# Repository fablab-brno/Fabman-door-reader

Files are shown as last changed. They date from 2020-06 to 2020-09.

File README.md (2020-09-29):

# Fabman door reader

This repository is for Fabman door reader. This device and firmware were designed and developed by FabLab Brno. 

You can find here: 
 - PCB data for all revision of HW 
 - STL files for case
 - design files of the case for Fusion 360
 - source code of the firmware for this device 
 - images of assembled board and images of the case
 
We used Arduino IDE for development of this firmware. 

You will need these libraries to compile FW from source code: 
 - ArduinoJson (v. 6.13.0 in Library Manager)
 - WiFiManager (https://github.com/tzapu/WiFiManager/tree/development)- install it in IDE from ZIP file
 - SimpletTimer (https://github.com/jfturcot/SimpleTimer) - install it in IDE from ZIP file
 - SmartLeds (https://platformio.org/lib/show/1740/SmartLeds) - install it in IDE from ZIP file

#### This firmware include following:

- [x] OTA update
- [x] WiFiManager - you can setup your WiFi network for OTA updates, API key for Fabman bridge, name of the device, ID of the device and if connection type (WiFi/Ethernet) 

If somebody swipe their card and device is properly set to use Fabman service, it will send standart query and behave on received data. There is also option (which we use, but it is not default behaviour) to check, if member has **any** actvive package, and if so,it will be allowd to use door. This behaviour must be set by bollean variable (checkOH in config.h file) and FW must recompiled and flashed again in to the device. I will try to add this as option via WiFiManager in the future.  
OTA updates are available, but you must have some server where you can store text and bin files. Device check for new FW update at every start. 

#### HW include following: 

 - RGB LED (WS2812B) - which indicate status of the device (breathing blue - idle, green - allowed access, red - denied access, orange - WiFiManager setup process)
 - 12V to 5V voltage converter based on MP1584EN
 - 3-pin connector for 12V power connection (+12V, GND, GND for lock)
 - 2-pin connector for security alarm (optional). This is normaly closed when cover is closed as screw is pushing towards tactile switch. If somebody open the cover, switch will be released and external alarm system should trigger some alert.    
 - Security button
 - 3-pin JST connector for RFID data. This one is connected to the GWIOT 7941E RFID module which sends data via UART connection (9600 bauds). There is 5V, DATA and GND.  
 - 5V DC relay G6L-1F-DC5 which connect GND to the lock in the door. Positive voltage must be connected to the door directly.
 - 4-pin connector for UART. There is 5V, GND, RX and TX connection and this connector is used for programming and debugging.
 - Reset button
 - Boot button
 - Setup button - if you hold this button when device is powered on or reseted, it will call function which will turn on AP mode in ESP32 and will fire up web server with default address **192.168.4.1**. 

You can find some images of the board, 3D printed case and whole assembly in **/img** folder.
  
#### There are these revision of the board:

**rev. A**

First version of the board. Step-down converter is not working (wrong layout). RGB LED need bodge wire to the IO4 on ESP32. Everything else is working. 

**rev. B** 

Step-down converter is now using reference design for MP1584EN. RGB LED connection fixed. Relay and 3-pin JST connector moved to bottom side to save some height. Added setup button for WiFiManager. Added 6-pin connector to connect LAN module via SPI bus. This was working but LAN module (ENC28J60) does not supprt SSL connection.

**rev. C**

6-pin connector changed for 14-pin connector which support LAN8720 module. This module is supported by Arduino-ESP32 development tools. This as tested and it is working. **This board does not support PoE**. 

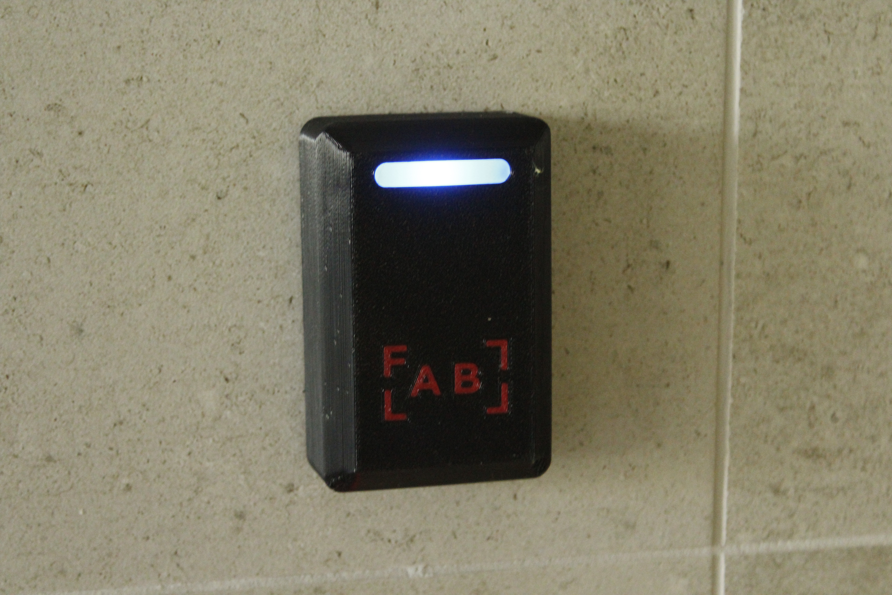
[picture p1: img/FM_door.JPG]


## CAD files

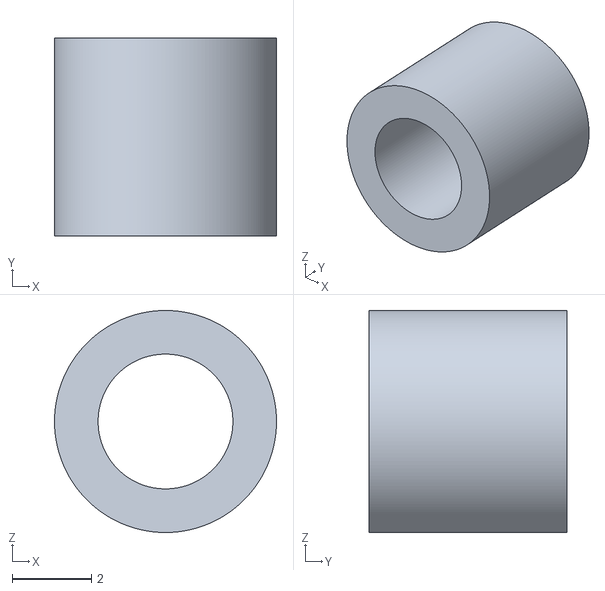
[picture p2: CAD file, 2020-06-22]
HW/STL/FM_door_standoff.stl
5.60 x 5.00 x 5.60

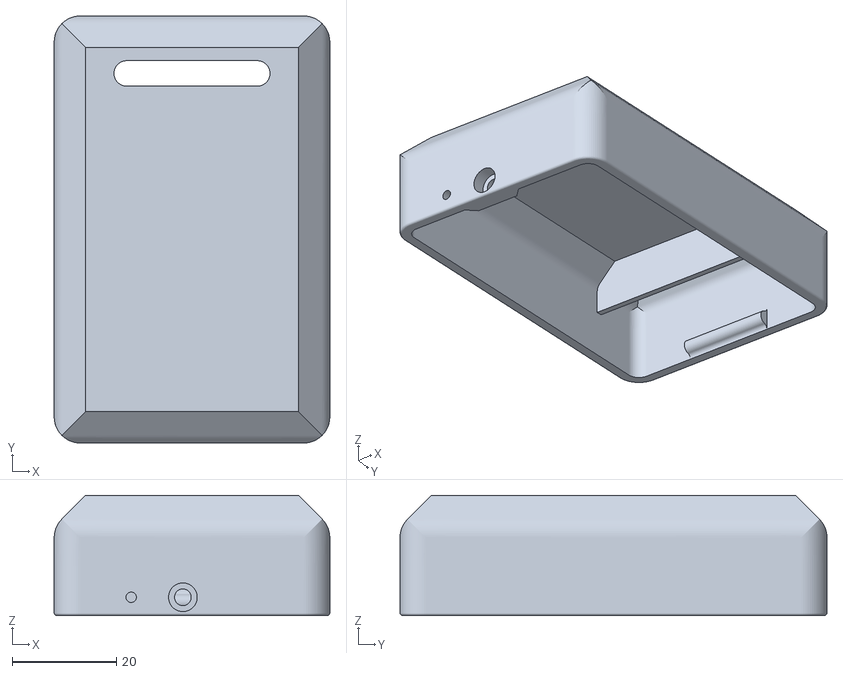
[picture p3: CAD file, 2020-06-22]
HW/STL/FM_door_front_cover_no_logo.stl
52.8 x 81.8 x 23.0

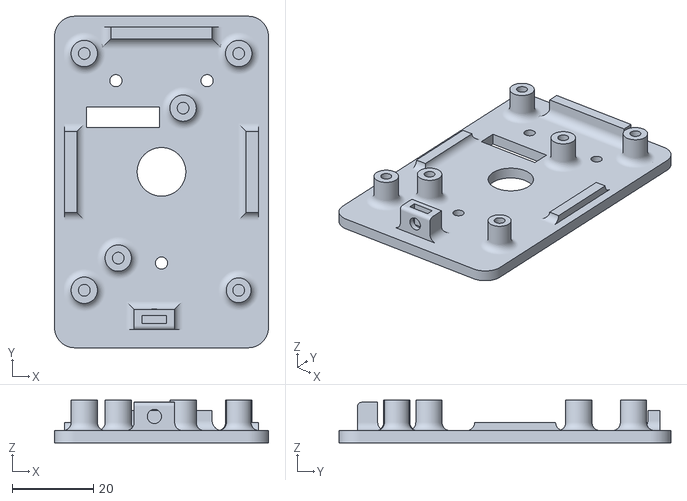
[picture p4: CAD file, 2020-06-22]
HW/STL/FM_door_back_plate.stl
52.8 x 81.8 x 10.5

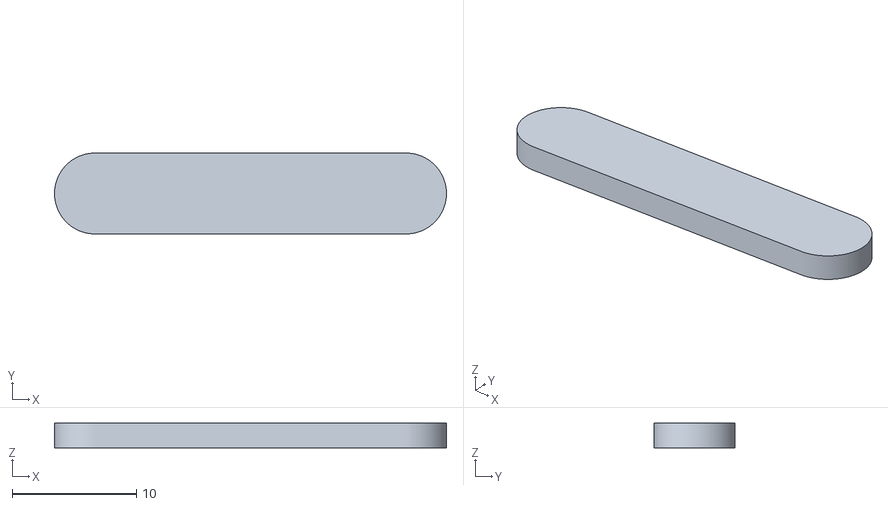
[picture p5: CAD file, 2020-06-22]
HW/STL/FM_door_diffusor.stl
31.5 x 6.50 x 2.00

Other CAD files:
HW/STL/FM_door_front_cover.stl
HW/FM_door_assembly.f3z

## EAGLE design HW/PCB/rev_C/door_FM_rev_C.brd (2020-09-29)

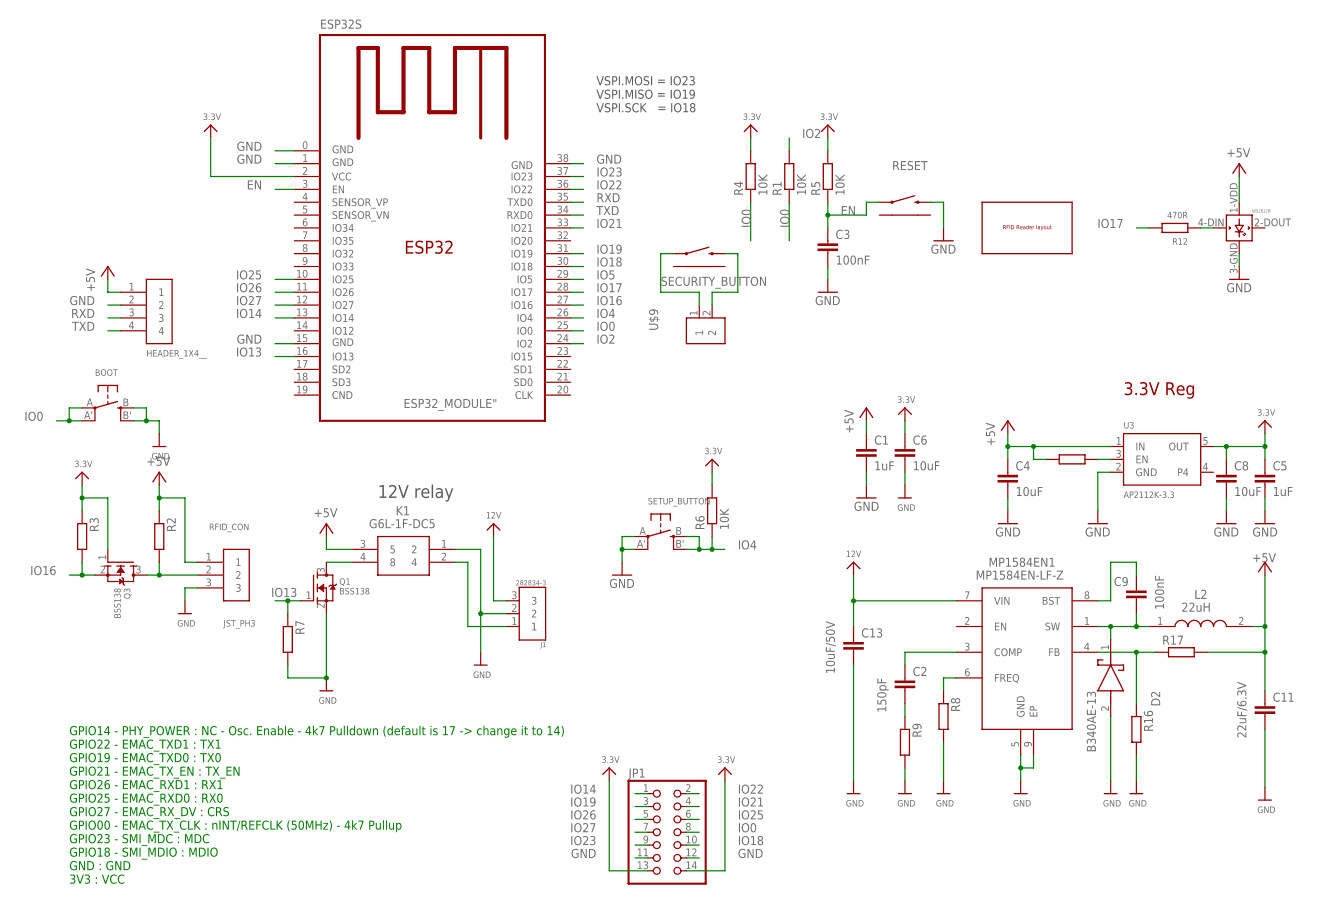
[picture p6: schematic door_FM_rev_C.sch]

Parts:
BOOT: BUTTON_KMR2_4.6X2.8
C1, C5: 1uF; C0805
C2: 150pF; C0805
C3, C9: 100nF; C0805
C4, C6, C8: 10uF; C0805
C11: 22uF/6.3V; C0805
C13: 10uF/50V; C1206
CN1: HEADER_1X4__; HEADER_1X4_RIGHT_ANGLE
D2: B340AE-13; DIOM5226X240N
ESP32S: ESP32_MODULE"; ESP32_MODULE
J1: 282834-3; TE_282834-3
JP1: PINHD-2X7SMT; 2X07_SMT
K1: G6L-1F-DC5
L2: 22uH; ASPI-0630LR
MP1584EN1: MP1584EN-LF-Z; SOIC127P600X170-9N
Q1, Q3: BSS138; SOT95P240X110-3
R1, R2, R3, R4, R5, R6, R7, R19: 10K; R0805
R8, R9: 100K; R0805
R12: 470R; R0805
R16: 40K2; R0805
R17: 210K; R0805
RESET: TACTILE_SWITCH_RIGHT_ANGLE_THT_; TACTILE_SWITCH_RIGHT_ANGLE_THT
RFID_CON: JST_PH3; JST-PH3
SECURITY_BUTTON: TACTILE_SWITCH_RIGHT_ANGLE_THT_; TACTILE_SWITCH_RIGHT_ANGLE_THT
SETUP_BUTTON: BUTTON_KMR2_4.6X2.8
U3: AP2112K-3.3; SOT95P290X120-5
U$9: 282834-2; CONN_282834-2
U$10: RFID_READER
WS2812B: WS2812B__; WS2812B_5050

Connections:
3.3V: C5.1, C6.1, C8.1, ESP32S.2 (VCC), JP1.13, JP1.14, Q3.1 (G), R3.1, R4.2, R5.2, R6.2, U3.5 (OUT)
12V: C13.1, J1.3, MP1584EN1.7 (VIN)
+5V: C1.1, C4.1, C11.1, CN1.1, K1.3 (5), L2.2, R2.1, R17.2, R19.1, RFID_CON.1, U3.1 (IN), WS2812B.1-VDD (VDD)
EN: C3.1, ESP32S.3 (EN), R5.1, RESET.1
GND: BOOT.B (S), BOOT.B' (S1), C1.2, C3.2, C4.2, C5.2, C6.2, C8.2, C11.2, C13.2, CN1.2, D2.2 (A), ESP32S.0 (GND), ESP32S.1 (GND), ESP32S.15 (GND), ESP32S.38 (GND), J1.2, JP1.11, JP1.12, K1.1 (2), MP1584EN1.5 (GND), MP1584EN1.9 (EP), Q1.2 (S), R7.2, R8.2, R9.2, R16.2, RESET.2, RFID_CON.3, SETUP_BUTTON.A, SETUP_BUTTON.A' (P1), U3.2 (GND), WS2812B.3-GND (GND)
IO0: BOOT.A, BOOT.A' (P1), ESP32S.25 (IO0), JP1.8, R1.1, R4.1
IO2: ESP32S.24 (IO2), R1.2
IO4: ESP32S.26 (IO4), R6.1, SETUP_BUTTON.B (S), SETUP_BUTTON.B' (S1)
IO5: ESP32S.29 (IO5)
IO13: ESP32S.16 (IO13), Q1.1 (G), R7.1
IO14: ESP32S.13 (IO14), JP1.1
IO16: ESP32S.27 (IO16), Q3.2 (S), R3.2
IO17: ESP32S.28 (IO17), R12.2
IO18: ESP32S.30 (IO18), JP1.10
IO19: ESP32S.31 (IO19), JP1.3
IO21: ESP32S.33 (IO21), JP1.4
IO22: ESP32S.36 (IO22), JP1.2
IO23: ESP32S.37 (IO23), JP1.9
IO25: ESP32S.10 (IO25), JP1.6
IO26: ESP32S.11 (IO26), JP1.5
IO27: ESP32S.12 (IO27), JP1.7
unnamed: K1.4 (8), Q1.3 (D)
unnamed: SECURITY_BUTTON.1, U$9.1
unnamed: SECURITY_BUTTON.2, U$9.2
unnamed: J1.1, K1.2 (4)
unnamed: Q3.3 (D), R2.2, RFID_CON.2
unnamed: R12.1, WS2812B.4-DIN (DIN)
unnamed: MP1584EN1.6 (FREQ), R8.1
unnamed: C2.2, R9.1
unnamed: R19.2, U3.3 (EN)
unnamed: C2.1, MP1584EN1.3 (COMP)
unnamed: MP1584EN1.4 (FB), R16.1, R17.1
unnamed: C9.2, D2.1 (K), L2.1, MP1584EN1.1 (SW)
unnamed: C9.1, MP1584EN1.8 (BST)
RXD: CN1.3, ESP32S.35 (TXD0)
TXD: CN1.4, ESP32S.34 (RXD0)

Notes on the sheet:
VSPI.MOSI = IO23 VSPI.MISO = IO19 VSPI.SCK = IO18
12V relay
3.3V Reg
GPIO14 - PHY_POWER : NC - Osc. Enable - 4k7 Pulldown (default is 17 -> change it to 14) GPIO22 - EMAC_TXD1 : TX1 GPIO19 - EMAC_TXD0 : TX0 GPIO21 - EMAC_TX_EN : TX_EN GPIO26 - EMAC_RXD1 : RX1 GPIO25 - EMAC_RXD0 : RX0 GPIO27 - EMAC_RX_DV : CRS GPIO00 - EMAC_TX_CLK : nINT/REFCLK (50MHz) - 4k7 Pullup G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

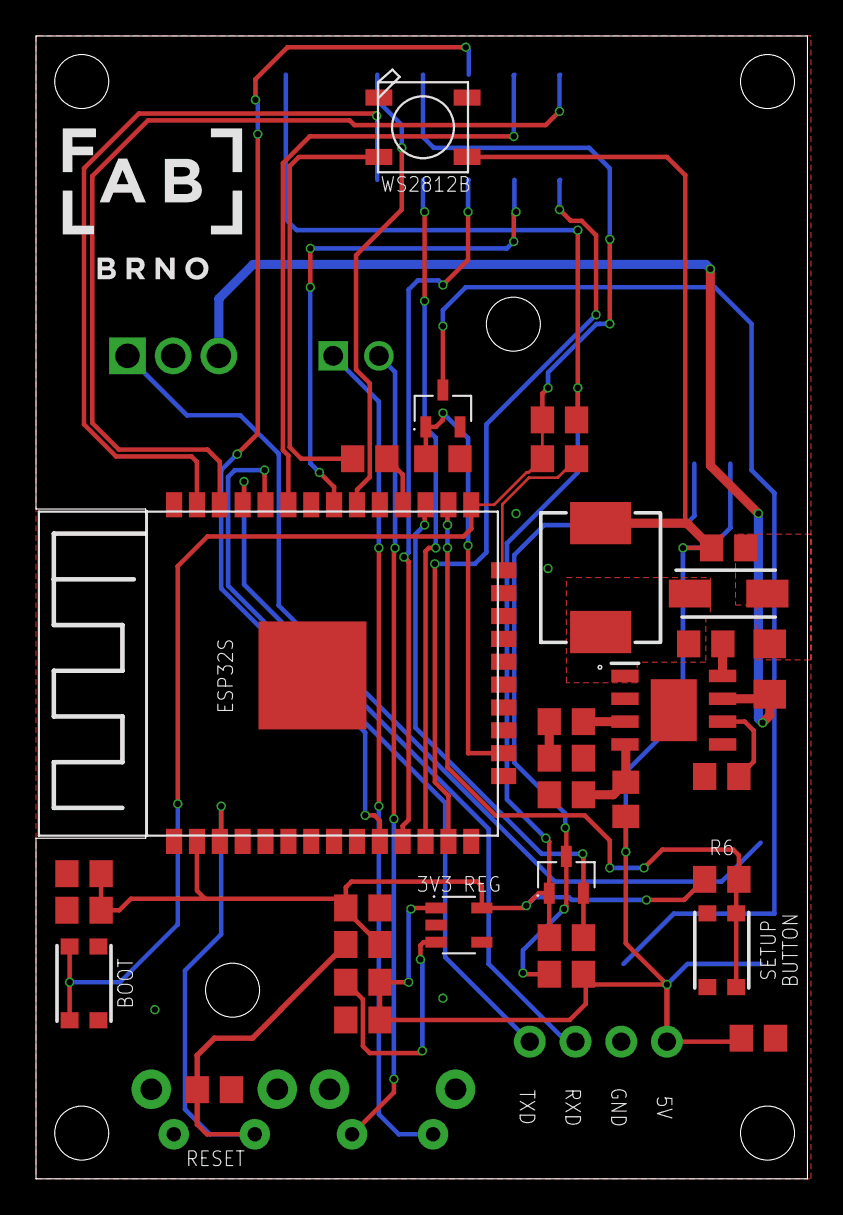
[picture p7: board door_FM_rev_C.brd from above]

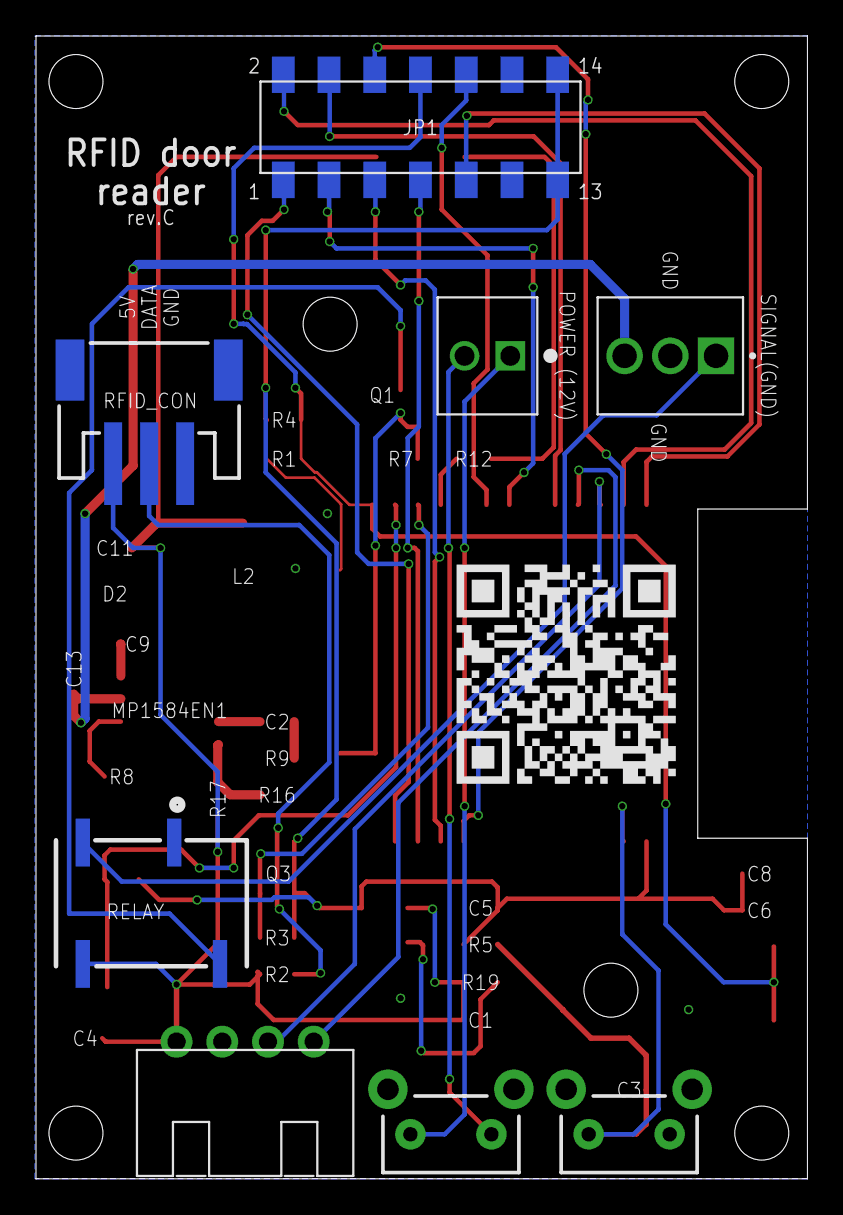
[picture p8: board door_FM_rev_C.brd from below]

Board: 2 copper layers, 42.9 x 63.5 mm, 42 parts (8 on the bottom side), 35 nets.

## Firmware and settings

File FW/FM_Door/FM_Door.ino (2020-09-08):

#include <WiFiMulti.h>
#include <HTTPClient.h>
#include <Preferences.h>
#include <ArduinoJson.h> // install it from Library Manager
#include <SimpleTimer.h> // install from ZIP: https://github.com/jfturcot/SimpleTimer
#include <ArduinoOTA.h>
#include <ESPmDNS.h>
#include <WiFiUdp.h>
#include <Update.h>
#include "FS.h"
#include "SPIFFS.h"
#include "esp_system.h"
#include "SPI.h"
#include "config.h"
#include "cert.h"
#include "wifimanager.h"
#include "RGB_led.h"
#include <NTPClient.h> //https://github.com/taranais/NTPClient

#include <ETH.h>

// Pin# of the enable signal for the external crystal oscillator (-1 to disable for internal APLL source)
#define ETH_PHY_POWER 14

// Type of the Ethernet PHY (LAN8720 or TLK110)
#define ETH_TYPE ETH_PHY_LAN8720

// I2C-address of Ethernet PHY (0 or 1 for LAN8720, 31 for TLK110)
#define ETH_ADDR 1
#define ETH_PHY_ADDR 1

// Pin# of the I2C clock signal for the Ethernet PHY
#define ETH_MDC_PIN 23

// Pin# of the I2C IO signal for the Ethernet PHY
#define ETH_MDIO_PIN 18

#define ETH_CLK_MODE ETH_CLOCK_GPIO0_IN

static bool eth_connected = false;

extern DynamicJsonDocument keyBuffer;

HardwareSerial RFID(2);

WiFiMulti wifiMulti;
SimpleTimer heartbeatTimer;
SimpleTimer wifiTimer;
SimpleTimer activityTimer;
SimpleTimer checkUser;
Preferences preferences;
WiFiUDP ntpUDP;
NTPClient timeClient(ntpUDP, "europe.pool.ntp.org", 3600, 60000); // change 3600 offset to your timezone

int wifiStatus;
byte data1 = 0;
String data2 = "";
bool setupButtonState = 0;
unsigned long currSessId;
unsigned long prevSessId;
bool online;
bool offline;
String firstName = "";
String lastName = "";
char* config_offlineKeys_token;
String offlineKeys;
String mac = "";
String API_key = "";
String machineName = "";
bool adminKey = 0;
int granted = 0;
int machineId;
int memberId;
bool useEthernet = 0;

WiFiClientSecure client;
HTTPClient http;
int httpResponseCode = 0;
String JSONinput = "";
String payload = "";
unsigned int configVersion;
unsigned int currentConfigVersion;

#define ARRAY_SIZE 20
String ssid[ARRAY_SIZE];
String pass[ARRAY_SIZE];
String SSIDString, passwordString = "";
bool resetSettings = 0;

void setup() {
  Serial.begin(115200);
  Serial.println("Starting serial..");

  preferences.begin("store", false);

  configVersion = preferences.getUInt("configVersion", 0);
  offlineKeys = preferences.getString("offlineKeys", "");
  API_key = preferences.getString("API_key", "");
  prevSessId = preferences.getULong("prevSessId", 0);
  machineName = preferences.getString("machineName", "");
  SSIDString = preferences.getString("SSIDString", "");
  passwordString = preferences.getString("passwordString", "");
  useEthernet = preferences.getBool("useEthernet", useEthernet);
  machineId = preferences.getInt("machineId", 0);

  preferences.end();

  if (useEthernet != 0) {
    mac = getMacAddress(1);
  } else {
    mac = getMacAddress(0);
  }

  Serial.println("MAC Address is: " + (mac));
  if (API_key != NULL) {
    Serial.println("Using API key from NVM.");
  } else {
    setAPIkey();
  }
  Serial.println("Name of the machine is: " + (machineName));
  Serial.println("FW version is: " + String(fwVersion) + "_&_" + String(__DATE__) + "_&_" + String(__TIME__));
  Serial.println("configVersion is: " + String(configVersion));
  Serial.println("offlineKeys: " + (offlineKeys));
  Serial.println("API key is : " + (API_key));
  Serial.println("Machine ID is: " + String(machineId));
  Serial.println("Previous session ID was: " + String(prevSessId));
  Serial.println("SSIDs are: " + SSIDString);
  Serial.println("passwords are: " + passwordString);

  RFID.begin(9600); // start serial to RFID reader
  Serial.println("FM version:" + (fwVersion));

  pinMode(relayPin, OUTPUT);
  digitalWrite(relayPin, LOW);

  setDevice();

  if (useEthernet != 0) {
    WiFi.onEvent(WiFiEvent);
    ETH.begin( PHY1 , 14, 23, 18 , ETH_PHY_LAN8720);
  } else {
    setWiFi();

    Serial.println("Connecting Wifi...");

    int8_t scanResult;
    scanResult = WiFi.scanNetworks();
    if (scanResult == 0) {
      Serial.println("No known WiFi found, going offline.");
      offline = 1;
    } else {
      connection();
    }
    wifiStatus = WiFi.status();
  }
  timeClient.begin();
  timeClient.update();

  Serial.print("configVersion is: ");
  Serial.println(configVersion);

  Serial.println("Swipe your card...");
  startShow(granted);
}

void setDevice() {

  // The extra parameters to be configured (can be either global or just in the setup)
  // After connecting, parameter.getValue() will get you the configured value
  // id/name placeholder/prompt default length
  machine_name_char[39] = '\0';
  api_key_char[39] = '\0';
  WiFiManagerParameter custom_device_name("device_name", "Device name (max 40 chars)", machine_name_char, 40);
  WiFiManagerParameter custom_api_key("API_key", "API key", api_key_char, 40);
  IntParameter custom_machine_id("machine_id", "Machine ID from Fabman", machine_id_int);
  IntParameter custom_use_lan("use_lan", "Use LAN port (0 = no, 1 = yes)", use_lan_int);

  //WiFiManager
  //Local intialization. Once its business is done, there is no need to keep it around
  WiFiManager wifiManager;

  //set config save notify callback
  wifiManager.setSaveConfigCallback(saveConfigCallback);

  wifiManager.addParameter(&custom_device_name);
  wifiManager.addParameter(&custom_api_key);
  wifiManager.addParameter(&custom_machine_id);
  wifiManager.addParameter(&custom_use_lan);

  //reset settings - for testing
  setupButtonState = digitalRead(setupButtonPin);
  if (setupButtonState == 0) { // right code for FL FM PCB
    //if (stopButtonState == 1) { //uncomment for testing on ESP32 dev board
    //    Serial.println("Calling WiFiManager resetSettings function");
    wifiManager.resetSettings();
    if (!wifiManager.autoConnect("FabmanAP")) {
      Serial.println("failed to connect and hit timeout");
      delay(3000);
      //reset and try again, or maybe put it to deep sleep
      ESP.restart();
      delay(5000);
    }
  }

  //read updated parameters
  strcpy(machine_name_char, custom_device_name.getValue());
  strcpy(api_key_char, custom_api_key.getValue());
  machine_name_char[39] = '\0';
  api_key_char[39] = '\0';
  machine_id_int = custom_machine_id.getValue();
  use_lan_int = custom_use_lan.getValue();
  String API_key(api_key_char); //convert char array to String
  String customName = (machine_name_char);

  Serial.println("Device name is: " + customName);
  Serial.println("API key is: " + API_key);
  Serial.println("Bridge ID from WM is: " + String(machine_id_int));
  Serial.println("Use LAN is: " + String(use_lan_int));

  //save the custom parameters to FS
  if (shouldSaveConfig) {
    Serial.println("Saving config from WiFiManager");
    Serial.println();

    preferences.begin("store", false);
    machineName = customName;
    preferences.putString("machineName", machineName);
    String API_key_ = "Bearer " + API_key;// combine predefined String "Bearer " with String from WiFiManager
    preferences.putString("API_key", API_key_);
    machineId = machine_id_int;
    preferences.putInt("machineId", machineId);
    useEthernet = use_lan_int;
    preferences.putBool("useEthernet", useEthernet);
    preferences.end();
    Serial.println("Custom parameters saved to preferences");
    //end save
  }
}

void device() {
  if ((granted == 1) && (relayOpen == 0) && ((millis() - lastRelayOpenTime) >= relayOpenTime)) {
    digitalWrite(relayPin, HIGH);
    Serial.println("Granted: " + String(granted));
    lastRelayOpenTime = millis();
    relayOpen = 1;
  }
  if ((relayOpen == 1) && ((millis() - lastRelayOpenTime) >= relayOpenTime)) {
    digitalWrite(relayPin, LOW);
    relayOpen = 0;
    sendStop();
  }
}

void checkLastDenied() {
  if (lastDenied == 1) {
    if ((millis() - lastLastDeniedTime) >= lastDeniedTime) {
      lastDenied = 0;
    }
  }
}

void clearGranted() {
  if ((granted == 1) || (granted == 2)) {
    if ((millis() - grantedTimoutLong) >= grantedTimeout) {
      granted = 0;
    }
  }
}

void WiFiEvent(WiFiEvent_t event)
{
  switch (event) {
    case SYSTEM_EVENT_ETH_START:
      Serial.println("ETH Started");
      //set eth hostname here
      ETH.setHostname("esp32-ethernet");
      break;
    case SYSTEM_EVENT_ETH_CONNECTED:
      Serial.println("ETH Connected");
      break;
    case SYSTEM_EVENT_ETH_GOT_IP:
      Serial.print("ETH MAC: ");
      Serial.print(ETH.macAddress());
      Serial.print(", IPv4: ");
      Serial.print(ETH.localIP());
      if (ETH.fullDuplex()) {
        Serial.print(", FULL_DUPLEX");
      }
      Serial.print(", ");
      Serial.print(ETH.linkSpeed());
      Serial.println("Mbps");
      eth_connected = true;
      online = 1;
      OTA();
      break;
    case SYSTEM_EVENT_ETH_DISCONNECTED:
      Serial.println("ETH Disconnected");
      eth_connected = false;
      break;
    case SYSTEM_EVENT_ETH_STOP:
      Serial.println("ETH Stopped");
      eth_connected = false;
      break;
    default:
      break;
  }
}

void loop() {
  readTags();
  heartbeatTimer.run();
  wifiTimer.run();
  checkLastDenied();
  device();
  neopixelLoop();
  clearGranted();
  if (granted == 0) {
    updateBreath();
  }
}

/*function which is called when device is not connected to network*/
void connection() {
  wifiStatus = WiFi.status();
  if (wifiStatus != WL_CONNECTED) {
    online = 0;
    Serial.println("Trying to connect.. ");
    Serial.println("");
    wifiMulti.run();
  } else if ((wifiStatus == WL_CONNECTED) && (online != 1)) {
    online = 1;
    Serial.println("WiFi connected");
    Serial.print("IP address: ");
    Serial.println(WiFi.localIP());
    Serial.println("Starting OTA..");
    OTA();
  }
}

/* parse Config version from JSON */
void get_configVersion() {
  DynamicJsonDocument jsonBuffer(2048);
  String JSONinput = payload;

  Serial.print("Config version payload: ");
  Serial.println(payload);

  //Serial.println(payload);
  Serial.println();
  deserializeJson(jsonBuffer, JSONinput);
  JsonObject root = jsonBuffer.as<JsonObject>();

  JsonObject config = root["config"];
  currentConfigVersion = root["config"]["configVersion"];
  JsonArray offlineKeys_array = config["offlineKeys"];
  for (offlineKeys : offlineKeys_array) {
    const char* token = offlineKeys["token"];
  }
  currentConfigVersion = root["config"]["configVersion"];
  Serial.print("currentConfigVersion which is read: ");
  Serial.println(currentConfigVersion);
  if (currentConfigVersion != 0) {
    if (currentConfigVersion != configVersion) {
      Serial.print("configVersion which is read: ");
      Serial.println(configVersion);
      preferences.begin("store", false);
      preferences.putUInt("configVersion", currentConfigVersion);
      preferences.end();
      Serial.println("Writing configVersion to NVS");
      configVersion = currentConfigVersion;
      offlineKeys = "";
      Serial.print("offlineKeys: ");
      Serial.println(offlineKeys);
      for (byte i = 0; i < offlineKeys_array.size(); i++) {
        const char* config_offlineKeys_token = offlineKeys_array[i]["token"];
        offlineKeys += config_offlineKeys_token;
        offlineKeys += (",");
      }
      preferences.begin("store", false);
      preferences.putString("offlineKeys", offlineKeys);
      preferences.end();
      Serial.println("Offline keys are stored in NVS");
      Serial.print("offlineKeys: ");
      Serial.println(offlineKeys);
      Serial.println();
      Serial.print("There should be total of ");
      Serial.print(offlineKeys_array.size());
      Serial.println(" keys.");
    }
  } else {
    Serial.println("No need to change configVersion in NVS");
  }
  Serial.println();
}


/* get String of device MAC address  */
String getMacAddress(bool device) { // 0 = wifi, 1 = ethernet
  uint8_t baseMac[6];
  // Get MAC address for WiFi station
  if (device == 1) {
    esp_read_mac(baseMac, ESP_MAC_ETH);
  } else {
    esp_read_mac(baseMac, ESP_MAC_WIFI_STA);
  }
  char baseMacChr[18] = {0};
  sprintf(baseMacChr, "%02X:%02X:%02X:%02X:%02X:%02X", baseMac[0], baseMac[1], baseMac[2], baseMac[3], baseMac[4], baseMac[5]);
  return String(baseMacChr);
}

/* Sorting devices by HW MAC address of ESP32 */
/* when is matching device not found, it will be used the Test machine, which should not be device in production enviroment */
void setAPIkey() {

  if (mac == "F4:CF:A2:82:FC:D4") {
    API_key = "Bearer some_API_key"; // First device
    machineName = "First device name";
    machineId = 0; //change this number with your real equipment number
    Serial.print("Set to ");
    Serial.println(machineName);
  }
  else if (mac == "F4:CF:A2:82:FC:EC") {
    API_key = "Bearer some_API_key"; // Second device
    machineName = "Second device name";
    machineId = 0; //change this number with your real equipment number
    Serial.print("Set to ");
    Serial.println(machineName);
  }
  else {
    API_key = "Bearer Second device name"; // Test machine
    machineName = "Test machine";
    machineId = 0; //change this number with your real equipment number
    Serial.print("Set to ");
    Serial.println(machineName);
  }
}

void wifiScan() {
  Serial.println("scan start");

  // WiFi.scanNetworks will return the number of networks found
  int n = WiFi.scanNetworks();
  Serial.println("scan done");
  if (n == 0) {
    Serial.println("no networks found");
  } else {
    Serial.print(n);
    Serial.println(" networks found");
    for (int i = 0; i < n; ++i) {
      // Print SSID and RSSI for each network found
      Serial.print(i + 1);
      Serial.print(": ");
      Serial.print(WiFi.SSID(i));
      Serial.print(" (");
      Serial.print(WiFi.RSSI(i));
      Serial.print(")");
      Serial.println((WiFi.encryptionType(i) == WIFI_AUTH_OPEN) ? " " : "*");
      delay(10);
    }
  }
  Serial.println("");
}

void setWiFi() {
  if (SSIDString != NULL) {
    for (int i = 0; i < ARRAY_SIZE; i++) {
      ssid[i] = getValue(SSIDString, ',', i);
      Serial.print(ssid[i] + " ");
    }
    Serial.println();
    for (int i = 0; i < ARRAY_SIZE; i++) {
      pass[i] = getValue(passwordString, ',', i);
      Serial.print(pass[i] + " ");
    }
    Serial.println();
    for (int i = 0; i < ARRAY_SIZE; i++) {
      wifiMulti.addAP(ssid[i].c_str(), pass[i].c_str());
      Serial.print("WiFi credentials are: " + pass[i] + "," + ssid[i]);
    }
  } else {
    wifiMulti.addAP("ssid", "pass");
    wifiMulti.addAP("ssid", "pass");
    wifiMulti.addAP("ssid", "pass");
    wifiMulti.addAP("ssid", "pass");
    wifiMulti.addAP("ssid", "pass");
    wifiMulti.addAP("ssid", "pass");
  }
}

// String  var = getValue( StringVar, ',', 2); // if  a,4,D,r  would return D
String getValue(String data, char separator, int index)
{
  int found = 0;
  int strIndex[] = { 0, -1 };
  int maxIndex = data.length();

  for (int i = 0; i <= maxIndex && found <= index; i++) {
    if (data.charAt(i) == separator || i == maxIndex) {
      found++;
      strIndex[0] = strIndex[1] + 1;
      strIndex[1] = (i == maxIndex) ? i + 1 : i;
    }
  }
  return found > index ? data.substring(strIndex[0], strIndex[1]) : "";
}  // END

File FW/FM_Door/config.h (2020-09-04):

// FW info
const String fwVersion = "0.1.0.2_beta";
String version_url  = "http://your_domain/door_version.txt";
String binURL = "http://your_domain/name_of_your.bin";

// Setup
const String API_key_user = "Bearer some_admin_key"; //admin key
const int setupButtonPin = 4;
const int relayPin = 13;
bool relayOpen = 0;
int relayOpenTime = 5000;
unsigned long lastRelayOpenTime = relayOpenTime;
bool lastDenied = 0;
int lastDeniedTime = 2000;
unsigned long lastLastDeniedTime = lastDeniedTime;
int grantedTimeout = 5000;
unsigned long grantedTimoutLong = grantedTimeout;
bool checkOH = 0; // if this value is 1, it will check for actual membership, not if member has any package

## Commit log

2020-06-22 FM door picture insert to the readme
2020-09-08 Added custom callbacks for setting up FM device
    - wifi settings
    - name of the bridge
    - ID of the bridge
    - bool for settings wifi or ethernet
2020-09-29 Readme update and added rev.C Eagle files
    [door_FM_rev_C.brd, door_FM_rev_C.sch]

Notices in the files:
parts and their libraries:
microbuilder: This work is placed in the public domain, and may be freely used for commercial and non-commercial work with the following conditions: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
